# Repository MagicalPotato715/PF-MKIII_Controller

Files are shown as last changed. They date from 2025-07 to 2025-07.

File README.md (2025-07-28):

****PF-MKIII_Controller****
-----

About: This is the handheld controller for the third-generation of my hexapod project: Pathfinder. This controller features left and right hall effect joysticks - for rotation and movement, respectively. There are also three latch buttons for ON/OFF control of autonomous movement, the hexapod, and the controller itself - alongside numerous miscellaneous status LEDs. Additionally, to communicate with the hexapod, the controller uses an NRF Chip as the main transmitter and an Arduino ESP32 Nano as the MCU. 
---

Why: Pathfinder MK-III itself has an NRF transmitter onboard. Since it's supposed to operate with Inverse Kinematics (live movement), the only options for controls are to either set up a wifi connection with a computer or through a controller. Since the hexapod's MCU, the STM32-f446re, doesn't support wireless code uploading, the only option is through a controller.
---

Screenshot 2025-07-28 at 10 32 58 AM
Screenshot 2025-07-28 at 10 33 16 AM
Screenshot 2025-07-28 at 10 33 49 AM

Bill Of Materials
-----
|Component|Quantity|Model|Lowest Price|Link|
|---|---|---|---|---|
|Dev Board|1|Arduino ESP32 Nano|$11.79|[Link](https://www.aliexpress.com/item/3256807939051766.html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)|
|Battery|1|3.7v lipo|$5.16|[Link](https://www.aliexpress.com/item/3256808941846105.html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)|
|Joysticks|2 (1x5pcs)|09032|$5.3|[Link](https://www.aliexpress.com/item/3256808542713532.html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)|
|NRF Transmitter|1|NRF24L01+|$2.30|[Link](https://www.aliexpress.com/item/3256805495903750.html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)|
|Latch Button|3 (1x10pcs)|6Pin Push Tactile|$1.29|[Link](https://www.aliexpress.com/item/2255800510764155.html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)|
|OLED Screen|1|SSD1306|$2.05|[Link](https://www.aliexpress.com/item/3256805954920554.html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)|
|Button|1|PBS-33B-G-X|$3.19|[Link](https://www.aliexpress.com/item/3256807265866776.html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)|
|RGB LED|2 (1x50pcs)|Common Cathode|$2.40|[Link](https://www.aliexpress.com/item/3256807678016250.html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)|
|Resistor Pack|1|510R, 44.7KR|$5.61|[Link](https://www.aliexpress.com/item/3256807883956541.html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)|
|10uF Capacitor|1|0805W106K250CC|$0.6|[Link](https://www.aliexpress.com/item/1626652703.html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)|
|0.1uF Capacitor|2 (1x100pcs)|0603B104K250SD|$0.95|[Link](https://www.aliexpress.com/item/1005003512666695.html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)|
|LED|2 (1x50pcs)|Green|$1.49|[Link](https://www.aliexpress.com/item/3256806082739727.html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)|
|PCB|1||$41.41|JLCPCB Order|

Total Components Price: $61.50
PCB Price: $41.41
Total Price: $102.91

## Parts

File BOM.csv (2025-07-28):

Component | Quantity | Model | Lowest Price | Link
Dev Board | 1 | Arduino ESP32 Nano | $11.79 | https://www.aliexpress.com/item/3256807939051766.html?mp=1
Battery | 1 | 3.7v lipo | $5.16 | https://www.aliexpress.com/item/3256808941846105.html?mp=1
Joysticks | 2 (1x5pcs) | 09032 | $5.3 | https://www.aliexpress.com/item/3256808542713532.html?mp=1
NRF Transmitter | 1 | NRF24L01+ | $2.30 | https://www.aliexpress.com/item/3256805495903750.html
Latch Button | 3 (1x10pcs) | 6Pin Push Tactile | $1.29 | https://www.aliexpress.com/item/2255800510764155.html?mp=1
OLED Screen | 1 | SSD1306 | $2.05 | https://www.aliexpress.com/item/3256805954920554.html?mp=1
Button | 1 | PBS-33B-G-X | $3.19 | https://www.aliexpress.com/item/3256807265866776.html?mp=1
RGB LED | 2 (1x50pcs) | Common Cathode | $2.40 | https://www.aliexpress.com/item/3256807678016250.html?mp=1
Resistor Pack | 1 | 510R, 44.7KR | $5.61 | https://www.aliexpress.com/item/3256807883956541.html
10uF Capacitor | 1 | 0805W106K250CC | $0.6 | https://www.aliexpress.com/item/1626652703.html
0.1uF Capacitor | 2 (1x100pcs) | 0603B104K250SD | $0.95 | https://www.aliexpress.com/item/1005003512666695.html
LED | 2 (1x50pcs) | Green | $1.49 | https://www.aliexpress.com/item/3256806082739727.html
PCB | 1 |  | $41.41 | JLCPCB Order

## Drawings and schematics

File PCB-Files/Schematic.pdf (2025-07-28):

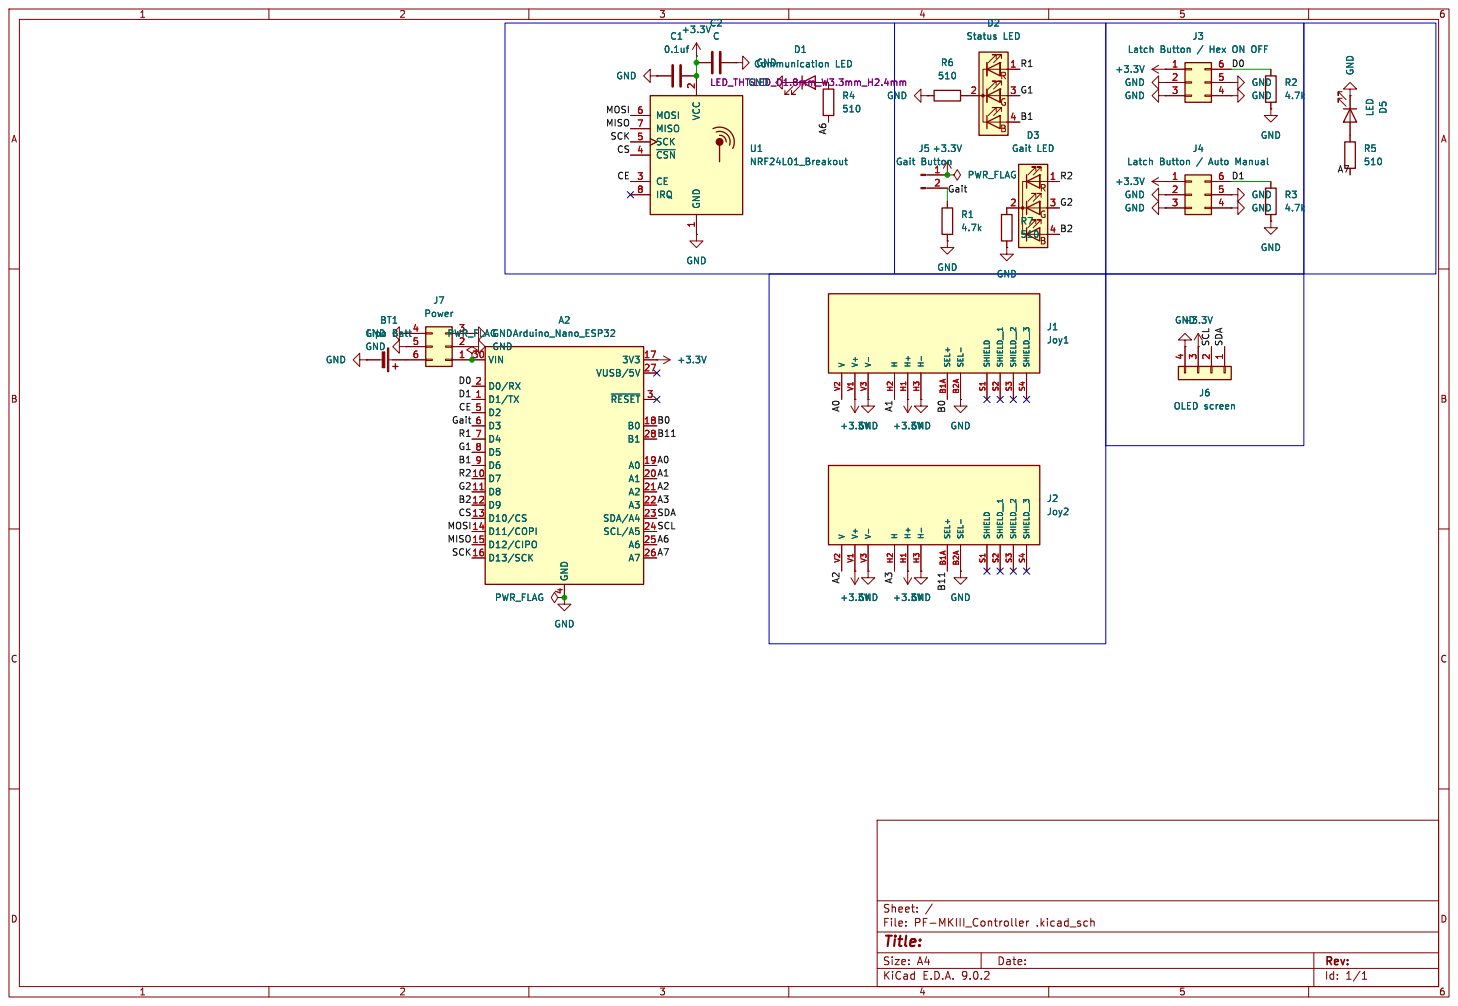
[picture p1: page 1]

Latch Button / Hex ON OFF
+3.3V GND
4 D3 Gait LED

1 U1 NRF24L01_Breakout MISO A6 G1 MOSI SCK MISO

Latch Button / Auto Manual 4

Latch Button / Auto Manual 1

Lipo Batt GND GND

V V2 V+ V1 V- V3 H H2 H+ H1 H- H3 SEL+ B1A SEL- B2A SHIELD S1 SHIELD__1 S2 SHIELD__2 S3 SHIELD__3 S4 GND

V V2 V+ V1 V- V3 H H2 H+ H1 H- H3 SEL+ B1A SEL- B2A SHIELD S1 SHIELD__1 S2 SHIELD__2 S3 SHIELD__3 S4 GND GND

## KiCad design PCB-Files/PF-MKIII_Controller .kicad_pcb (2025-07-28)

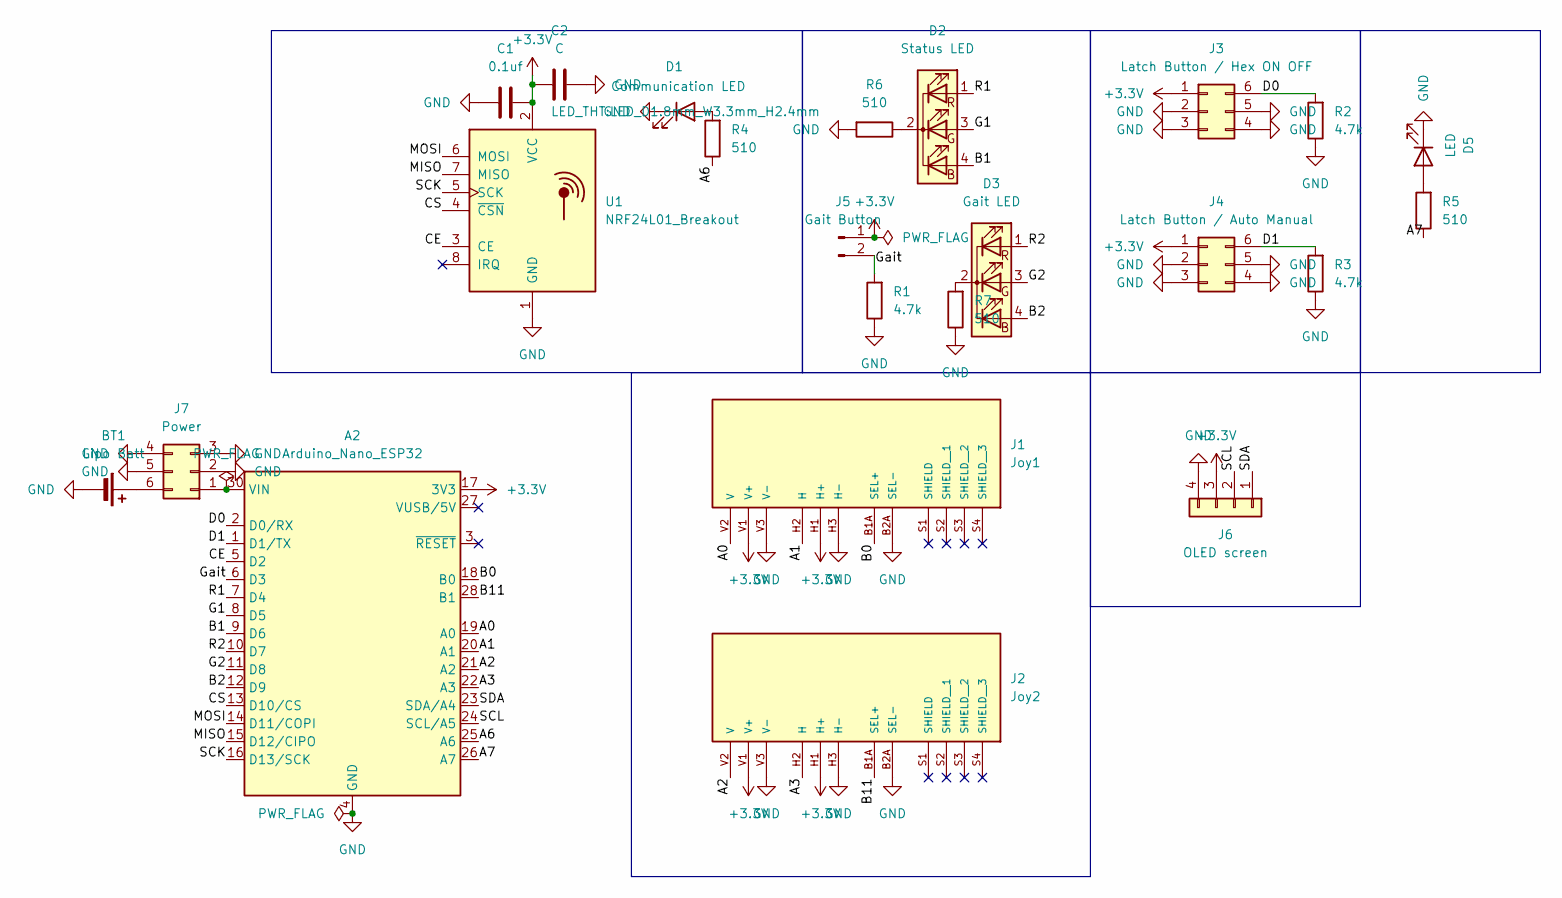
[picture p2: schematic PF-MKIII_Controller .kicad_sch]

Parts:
A2: Arduino_Nano_ESP32; Arduino_Nano
BT1: Lipo Batt; JST_PH_B2B-PH-K_1x02_P2.00mm_Vertical
C1: 0.1uf; C_0603_1608Metric
C2: C; C_0805_2012Metric
D1: Communication LED; LED_D1.8mm_W3.3mm_H2.4mm
D2: Status LED; LED_D5.0mm-4_RGB
D3: Gait LED; LED_D5.0mm-4_RGB
D5: LED; LED_D1.8mm_W3.3mm_H2.4mm
J1: Joy1; XDCR_COM-09032; PARTREV N/A
J2: Joy2; XDCR_COM-09032; PARTREV N/A
J3: Latch Button / Hex ON OFF; SW_DPDT_XLX
J4: Latch Button / Auto Manual; SW_DPDT_XLX
J5: Gait Button; PinHeader_1x02_P1.00mm_Vertical
J6: OLED screen; SSD1306_0.96_Oled
J7: Power; SW_DPDT_XLX
R1, R2, R3: 4.7k; R_Axial_DIN0204_L3.6mm_D1.6mm_P7.62mm_Horizontal
R4, R5, R6, R7: 510; R_Axial_DIN0204_L3.6mm_D1.6mm_P7.62mm_Horizontal
U1: NRF24L01_Breakout; nRF24L01_Breakout

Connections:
+3.3V: A2.17 (3V3), C1.2, C2.1, J1.H1 (H+), J1.V1 (V+), J2.H1 (H+), J2.V1 (V+), J3.1, J4.1, J5.1, J6.3, U1.2 (VCC)
/A0: A2.19 (A0), J1.V2 (V)
/A1: A2.20 (A1), J1.H2 (H)
/A2: A2.21 (A2), J2.V2 (V)
/A3: A2.22 (A3), J2.H2 (H)
/A6: A2.25 (A6), R4.1
/A7: A2.26 (A7), R5.1
/B0: A2.18 (B0), J1.B1A (SEL+)
/B1: A2.9 (D6), D2.4 (BA)
/B2: A2.12 (D9), D3.4 (BA)
/B11: A2.28 (B1), J2.B1A (SEL+)
/CE: A2.5 (D2), U1.3 (CE)
/CS: A2.13 (D10/CS), U1.4 (~CSN)
/D0: A2.2 (D0/RX), J3.6, R2.2
/D1: A2.1 (D1/TX), J4.6, R3.2
/G1: A2.8 (D5), D2.3 (GA)
/G2: A2.11 (D8), D3.3 (GA)
/Gait: A2.6 (D3), J5.2, R1.2
/MISO: A2.15 (D12/CIPO), U1.7 (MISO)
/MOSI: A2.14 (D11/COPI), U1.6 (MOSI)
/R1: A2.7 (D4), D2.1 (RA)
/R2: A2.10 (D7), D3.1 (RA)
/SCK: A2.16 (D13/SCK), U1.5 (SCK)
/SCL: A2.24 (SCL/A5), J6.2
/SDA: A2.23 (SDA/A4), J6.1
GND: A2.4 (GND), A2.29 (GND), BT1.2 (-), C1.1, C2.2, D1.1 (K), D5.1 (K), J1.B2A (SEL-), J1.H3 (H-), J1.V3 (V-), J2.B2A (SEL-), J2.H3 (H-), J2.V3 (V-), J3.2, J3.3, J3.4, J3.5, J4.2, J4.3, J4.4, J4.5, J6.4, J7.2, J7.3, J7.4, J7.5, R1.1, R2.1, R3.1, R6.2, R7.1, U1.1 (GND)
unnamed: A2.30 (VIN), J7.1
unnamed: BT1.1 (+), J7.6
unnamed: D1.2 (A), R4.2
unnamed: D2.2 (K), R6.1
unnamed: D3.2 (K), R7.2
unnamed: D5.2 (A), R5.2

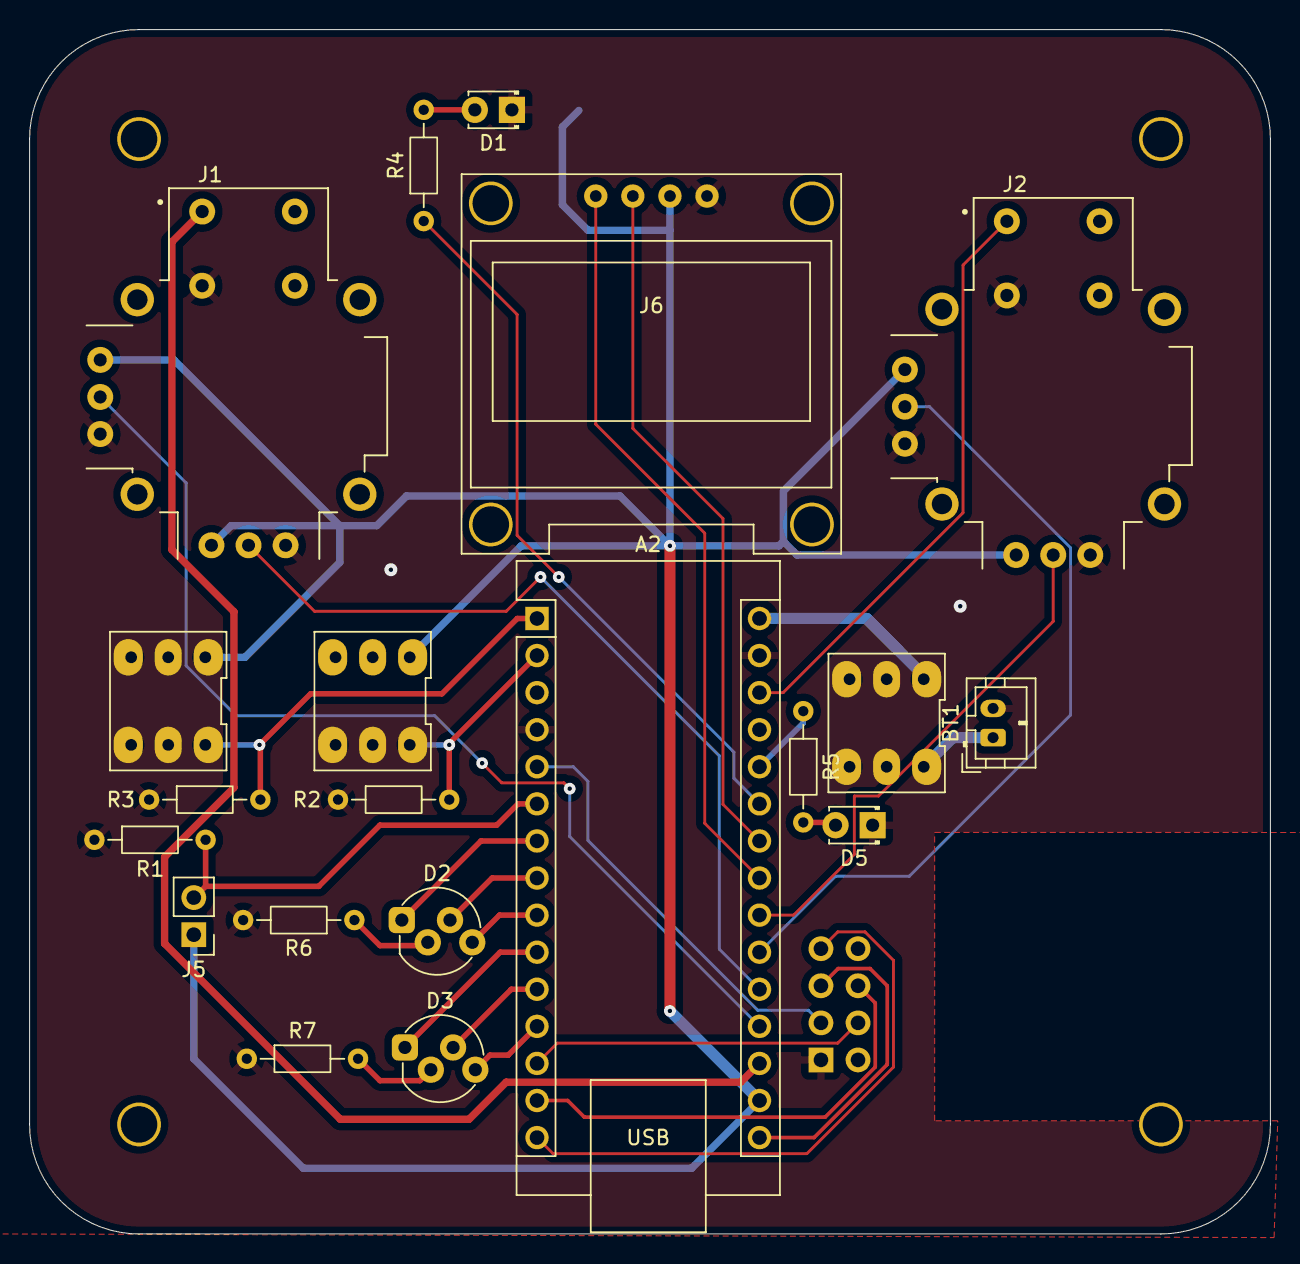
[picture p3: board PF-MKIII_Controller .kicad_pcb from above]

Board: 2 copper layers, 85.0 x 82.5 mm, 21 parts (1 on the bottom side), 32 nets.

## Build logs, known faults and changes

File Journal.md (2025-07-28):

---
title: "Pathfinder MK-III Handheld Controller"
author: "Calvin Hung"
description: "This is the handheld controller for my hexapod robotics project Pathfinder MKIII. Learn more about Pathfinder MK-III here: https://github.com/MagicalPotato715/Pathfinder-MKIII."
created_at: "7/20/2025"
total time spent: "16 hours"
---

# July 21th: Planning & Research

After searching and deliberation (thinking takes a lot of time), here's the list I came up with for the complete setup.

Hardware:
- Raspberry Pi Pico RP2040 for control
- Left Joystick Rotation
- Right Joystick Movement
- OLED screen for misc displays
- Latch button for Hexapod ON/OFF
- Latch button for eventual Autonomous/Manual
- Momentary Button + LED for Gait Switching
- Lipo + P-Fet system for power from lipo while using USB-C coding
- Comical ON/OFF switch for controller on off
- RGB Status LED for Hexapod Status (On/off/lowpower?)
- NRF24L01+ Reciever to talk to hexapod
- LED to show connection of NRF chip

Software:
- Code Main: take info from buttons etc and transfer to nrf chip.
- LEDs to show hexapod functionality/issues.
- Gait switching shown on OLED
- Gait switching -> each press rotates

This is the (not so) block diagram:
Screenshot 2025-07-21 at 3 24 50 PM

**Total time spent: 3h**

# July 22th: Begin Schematic & Making Symbols

Learning from my mistakes with the hexapod PCB, I decided to scout out the components (and a seller) before placing them down in Kicad. However, having the block diagram makes it a lot easier to know what to put.

Finished placing down the components! Time to make connections!
Screenshot 2025-07-21 at 7 52 32 PM

I decided to replace the KY-023 joysticks with these other ps5 joysticks. These new ones don't have a specific part number, but they atleast have a concrete footprint.
COM-09032_sml
Screenshot 2025-07-22 at 3 04 10 PM

I followed this schematic for the joystick wiring.
Screenshot 2025-07-22 at 3 44 41 PM

I also decided to replace the Raspberry Pi Pico with an Arduino ESP32 Nano, because the Pico didn't have enough analog pins. As it turns out, the Arduino ESP32 Nano has exactly what I need!

Chef's kiss
Screenshot 2025-07-22 at 7 53 50 PM

**Total time spent: 4h**

# July 23rd: Footprint search

I'm having trouble finding the right footprints for the switches I'll be using. For the On/Off switch, the issue seems to be with the pins being "panel mounted". Later, I managed to find a footprint for the 6-pin latch buttons with the help of the Kicad forum: https://www.google.com/search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.

2491cde89c9909adfb2831cac1cb1ce7448dc5d9_2_690x338

I finally found footprints for everything! I decided against using the rocker switch and replaced it with the latching button.
Screenshot 2025-07-23 at 10 07 40 PM

**Total time spent: 2h**

# July 25th: Layout & Routing

I began making the layout today! I also found out that I could place components (like the NRF chip) on the back side to save space! The block diagram helped, but some component placements had to differ from it because of the Arduino nano's pinouts.

This is after layout and before routing.
Screenshot 2025-07-25 at 3 03 40 PM

Screenshot 2025-07-25 at 10 54 22 PM
UGHHHH why do so many components overlap?
I discovered that the solution to a lot of overlap is: lots, and lots, and lots of vias.
However, I haven't finished routing because it's getting late.

**Total time spent: 3h**

# July 26th: DRC & finishing

I spent the first part of today working out the DRC kinks. I had to switch around many different sizings such as vias and traces. After DRC got worked out, I added curves to the edge cuts and tweaked the ground pours.

Screenshot 2025-07-27 at 10 48 14 AM

Update: after uploading photos of my layout to ChatGPT, I found out that I realized I placed the nrf chip completely wrong... As it turns out, I need decoupling capacitors and make the traces short.

These bad boys.
Screenshot 2025-07-28 at 9 58 04 AM

Below is the new NRF setup, with two decoupling capacitors, continuous traces, and a pour gap zone where the antenna is.
Screenshot 2025-07-28 at 9 59 21 AM

Now it's just about finished!

**Total time spent: 4h**

Screenshot 2025-07-28 at 10 08 41 AM

Screenshot 2025-07-28 at 10 08 59 AM
